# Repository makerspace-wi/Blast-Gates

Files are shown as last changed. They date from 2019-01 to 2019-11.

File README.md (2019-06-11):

# Blast-Gates
Schieberanordnung für Absauganlage

Die letzte geplante Variante konnte leider nicht realisiert werden - ein alternativ Vorschlag wurde erarbeitet.
<br>
Die Arbeiten wurden jetzt vollständig vom 'Dream-Team' übernommen und das Konzept wie folgt geändert:
<br><br>
Zum Einsatz kommt eine 'Distribution Box' aus Holz mit 6 Öffnungen, wobei die obere Öffnung eine Plexiglasscheibe sein wird, durch die man ins Innere schauen und ggf. zur Reinigung öffnen kann.

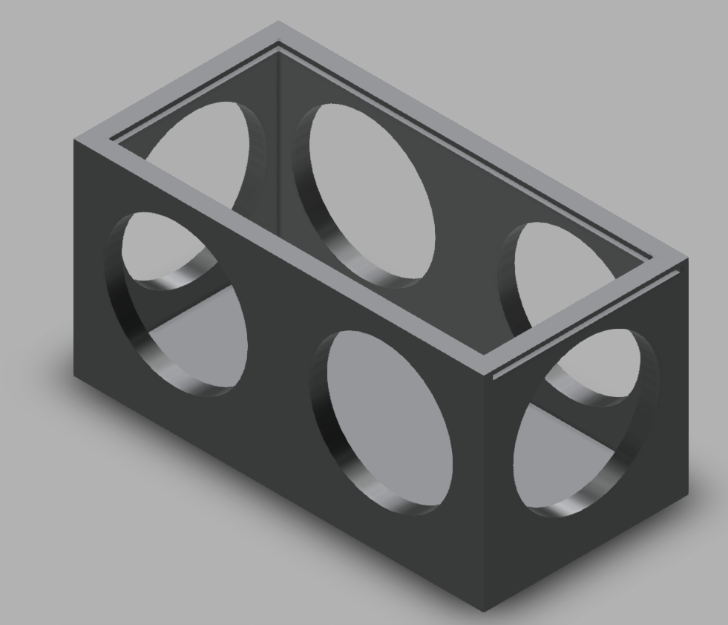
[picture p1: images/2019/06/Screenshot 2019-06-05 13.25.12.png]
  

Eine Öffnung wird an die Absaugeinrichtung angschlossen, jeweils eine von 4 Öffnungen gehen an die Formatkreissäge, die Bandsäge, den Abrichthobel, die Schleifvorrichtung und die letzte Öffnung ist für einen Handabsaugschlauch vorgesehen.<br>
Als Anschlüsse haben wir uns für industriell gefertigte, manuelle Schieber aus Aluguß/Stahlblech entschieden.

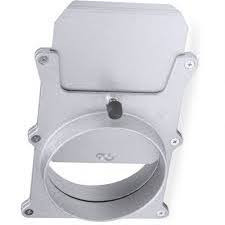
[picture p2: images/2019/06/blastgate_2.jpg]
  

In der ersten Ausbaustufe sollen die Schieber noch per Hand geöffnet/geschlossen werden, allerdings wird die Stellung jeder Klappe über Mikroschalter an eine Steuereinheit gemeldet.<br>
Zu einem späteren Zeitpunkt sollen die Schieber per Spindelantrieb elektronisch auf und zu gefahren werden.

<video width="320" height="240" controls>
  <source src='images/2019/06/BlastGateMetall.mp4' type="video/mp4">
</video>

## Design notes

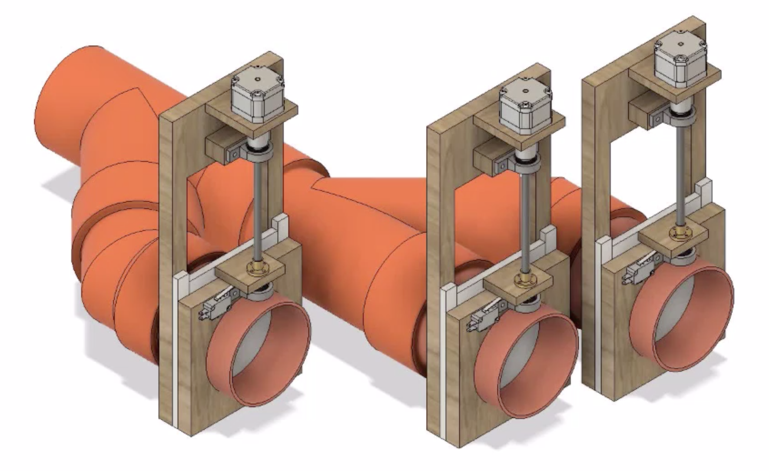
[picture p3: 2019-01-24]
images/2019/01/Screenshot 2019-01-24 10.25.47.png

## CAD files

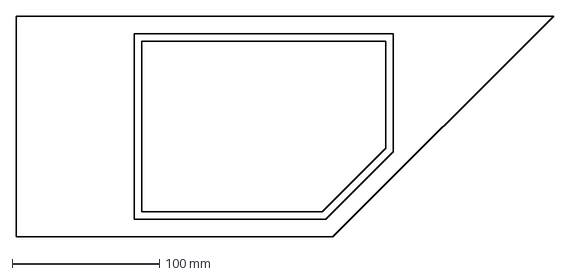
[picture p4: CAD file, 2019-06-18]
doc/AbsaubungsVerteiler/SeitenplatteLiAussparung.dxf
365.0 x 150.0 mm

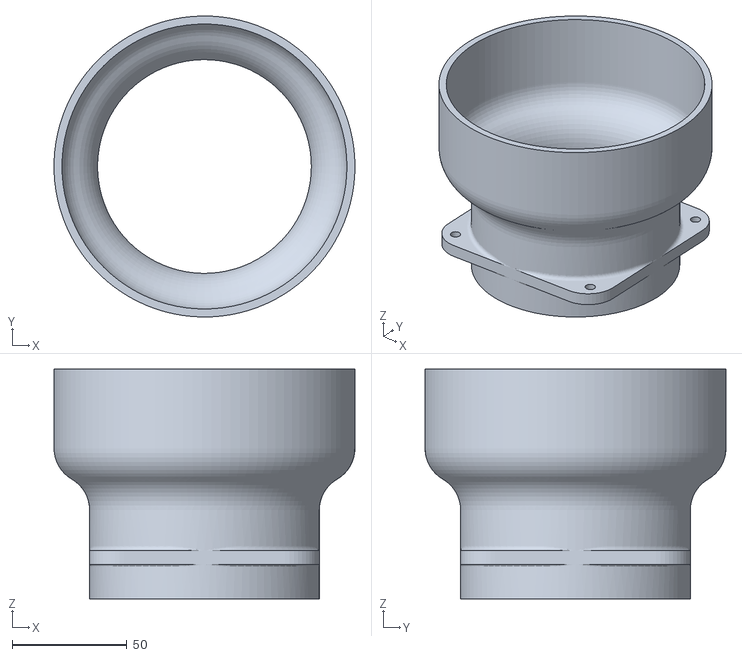
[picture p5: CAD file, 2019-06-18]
doc/AbsaubungsVerteiler/Reduzierstücke_mit_Halter.stl
131.0 x 131.0 x 100.0

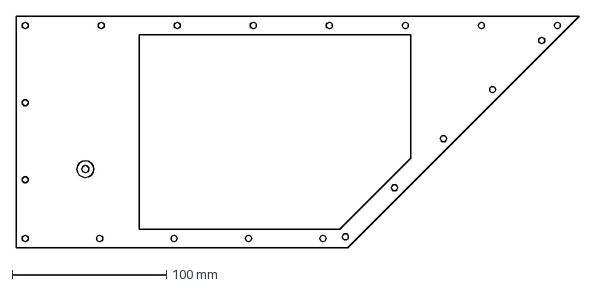
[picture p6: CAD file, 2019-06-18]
doc/AbsaubungsVerteiler/SeitenplatteLiGeh.dxf
365.0 x 150.0 mm

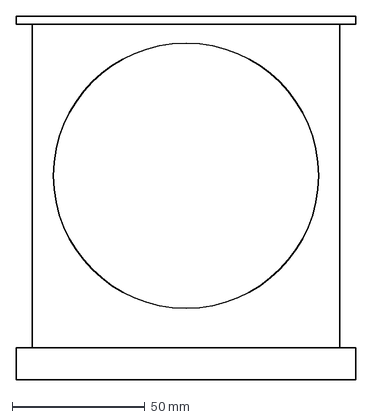
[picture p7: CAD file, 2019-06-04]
doc/AbsaubungsVerteiler/SeitenteilRechts.dxf
128.0 x 137.2 mm

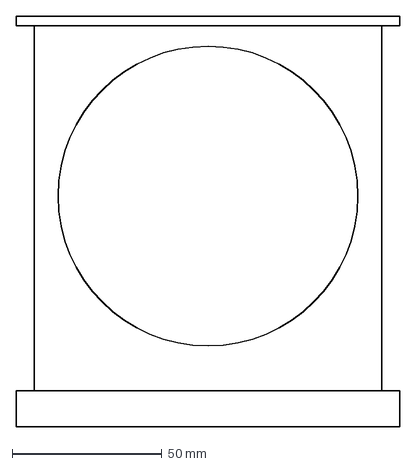
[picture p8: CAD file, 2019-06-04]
doc/AbsaubungsVerteiler/SeitenteilLinks.dxf
128.0 x 137.0 mm

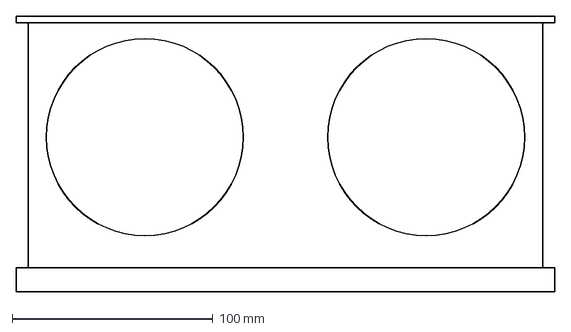
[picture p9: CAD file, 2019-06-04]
doc/AbsaubungsVerteiler/SeitenteilGross.dxf
268.0 x 137.2 mm

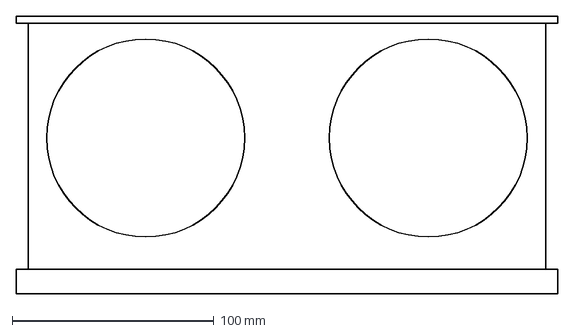
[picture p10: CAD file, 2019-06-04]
doc/AbsaubungsVerteiler/SeitenteilGrossN.dxf
268.0 x 137.2 mm

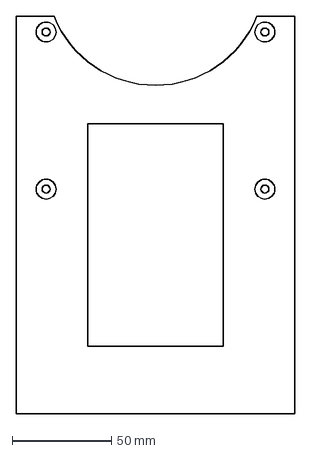
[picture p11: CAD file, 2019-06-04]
doc/AbsaubungsVerteiler/EndSchalterMount.dxf
140.0 x 200.0 mm

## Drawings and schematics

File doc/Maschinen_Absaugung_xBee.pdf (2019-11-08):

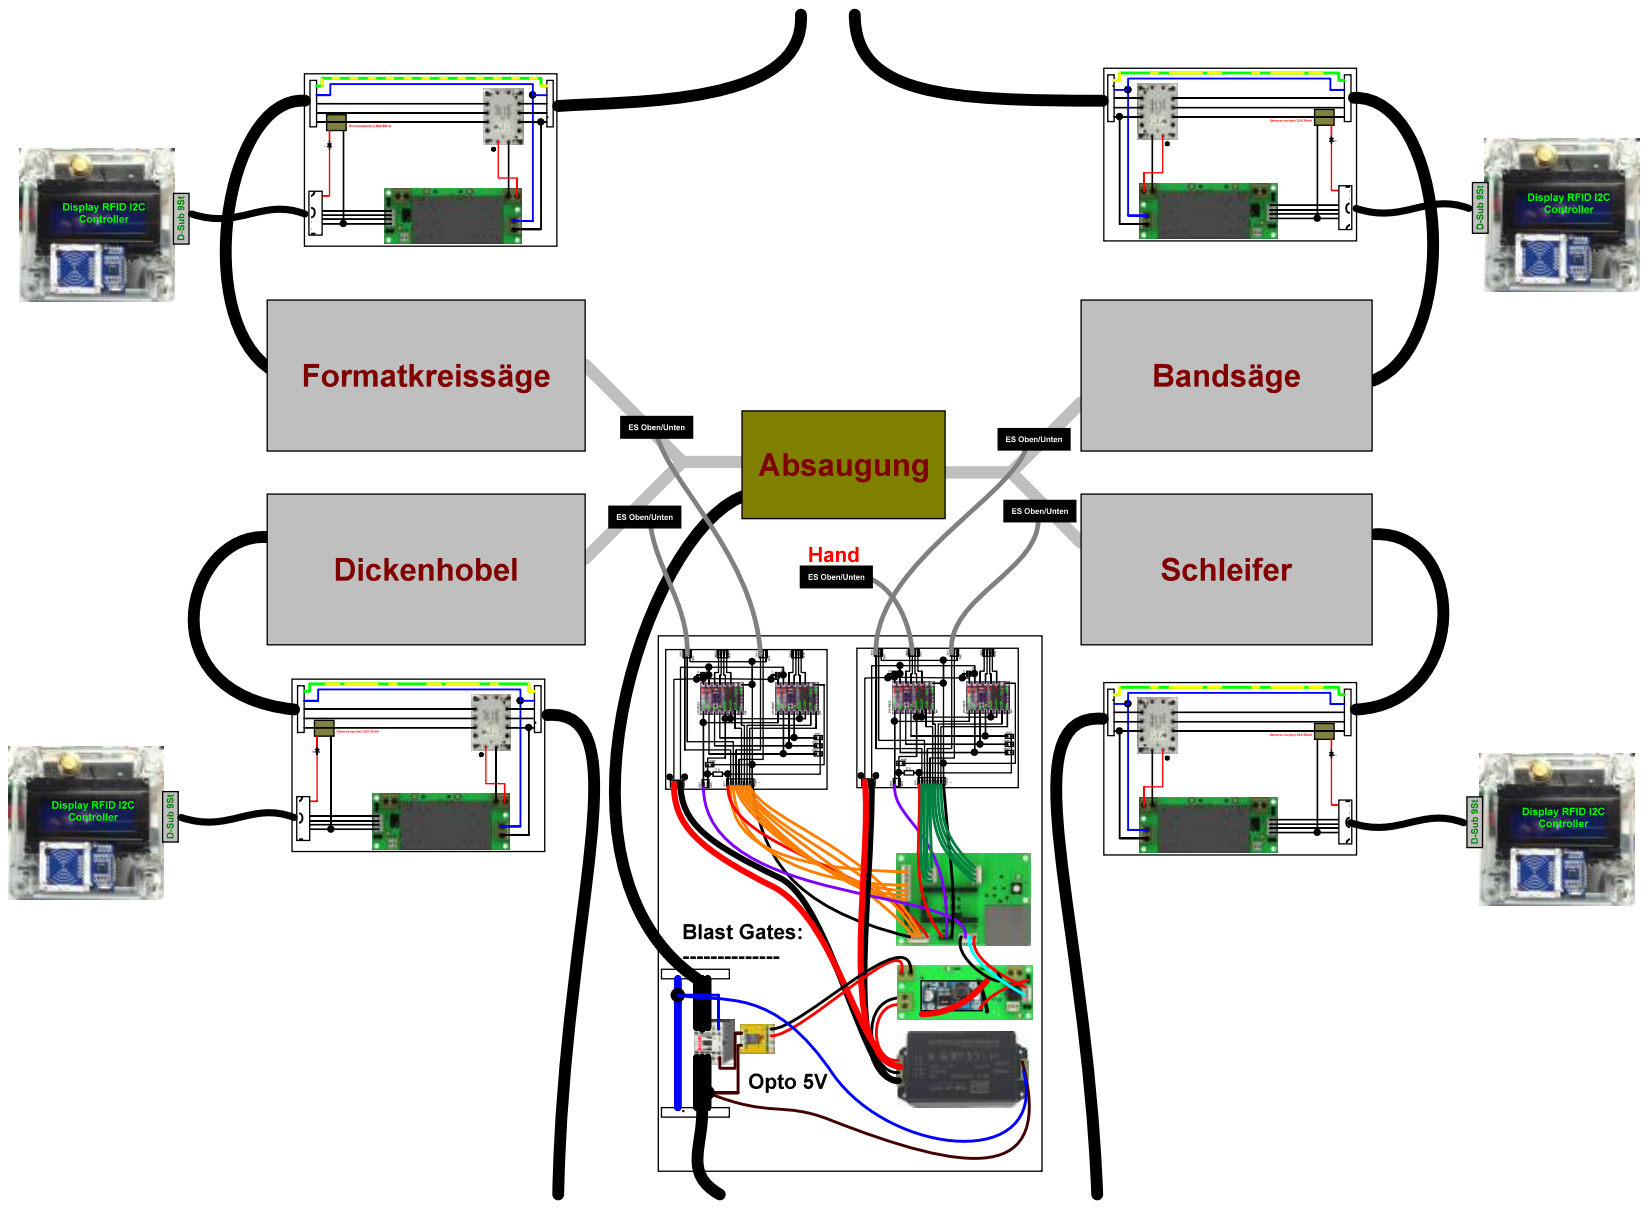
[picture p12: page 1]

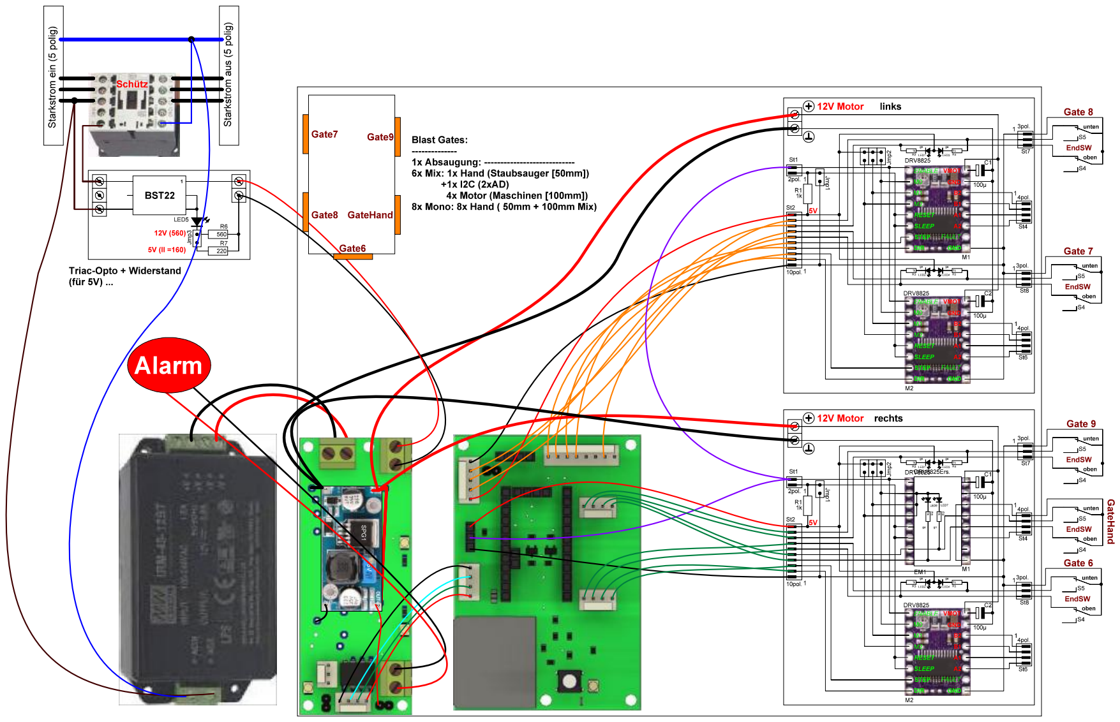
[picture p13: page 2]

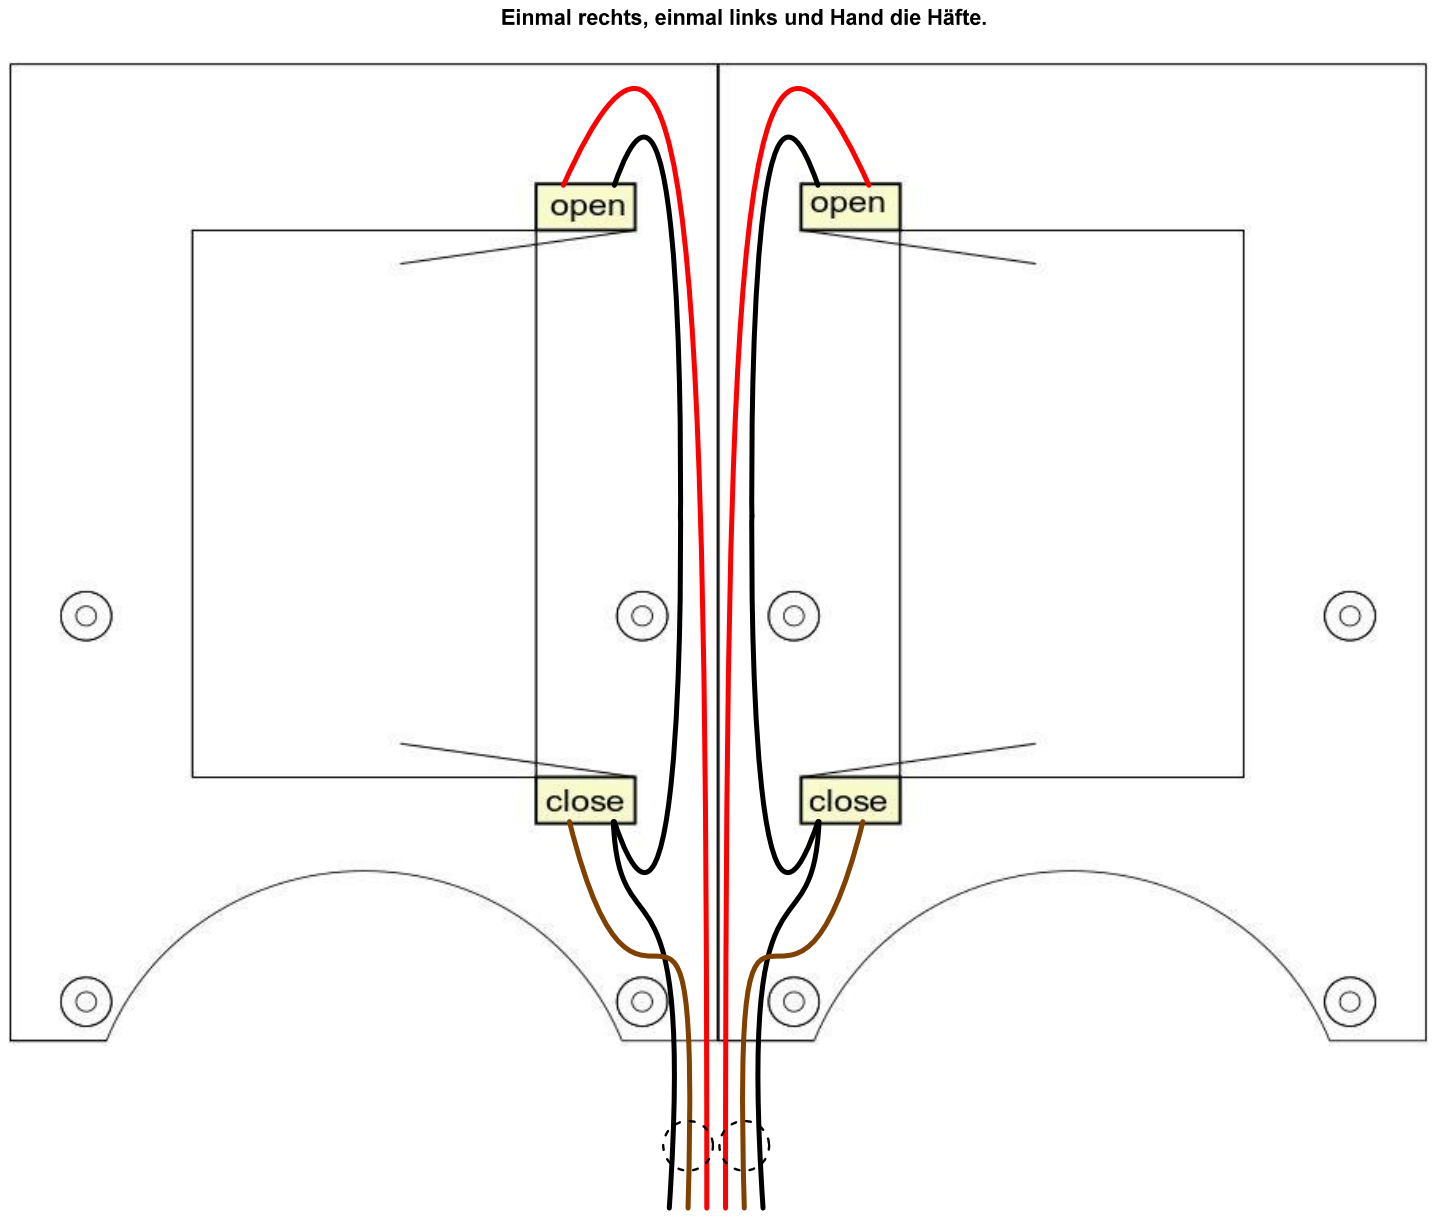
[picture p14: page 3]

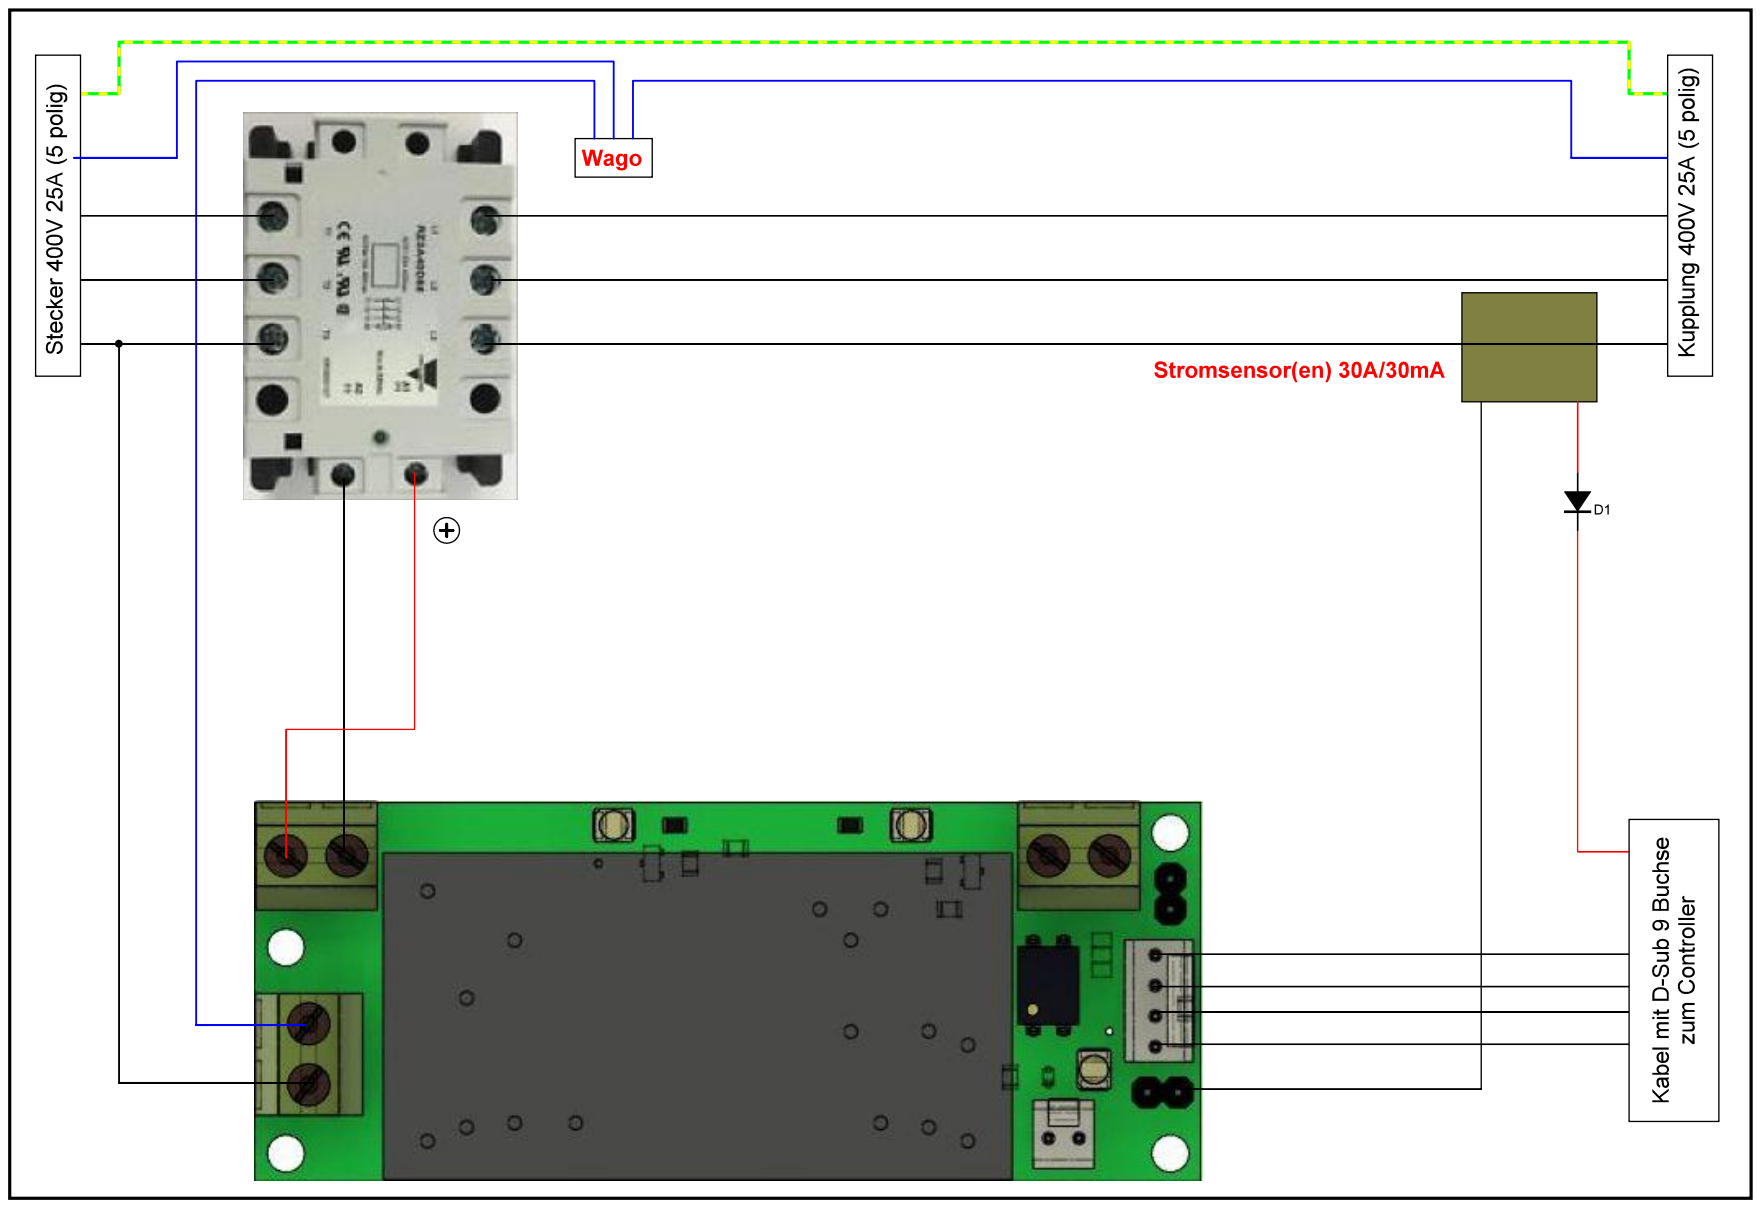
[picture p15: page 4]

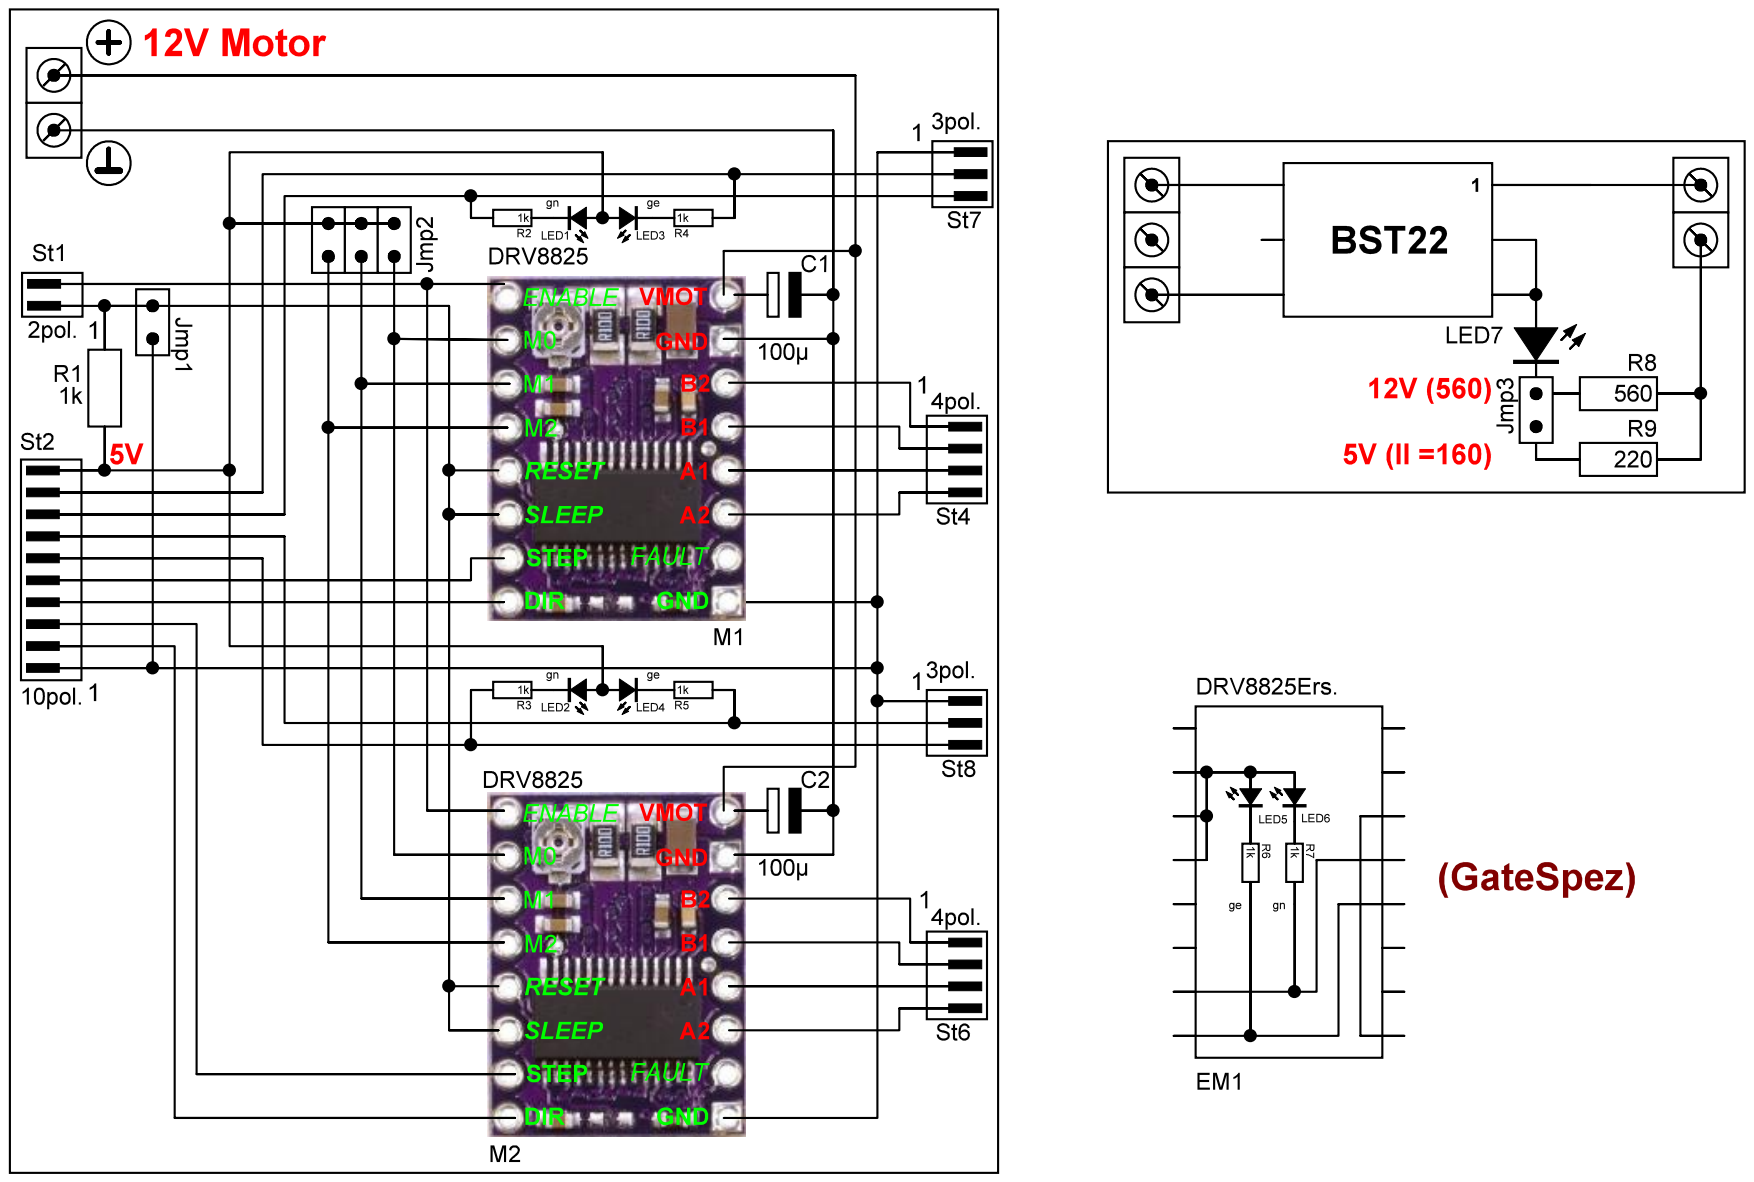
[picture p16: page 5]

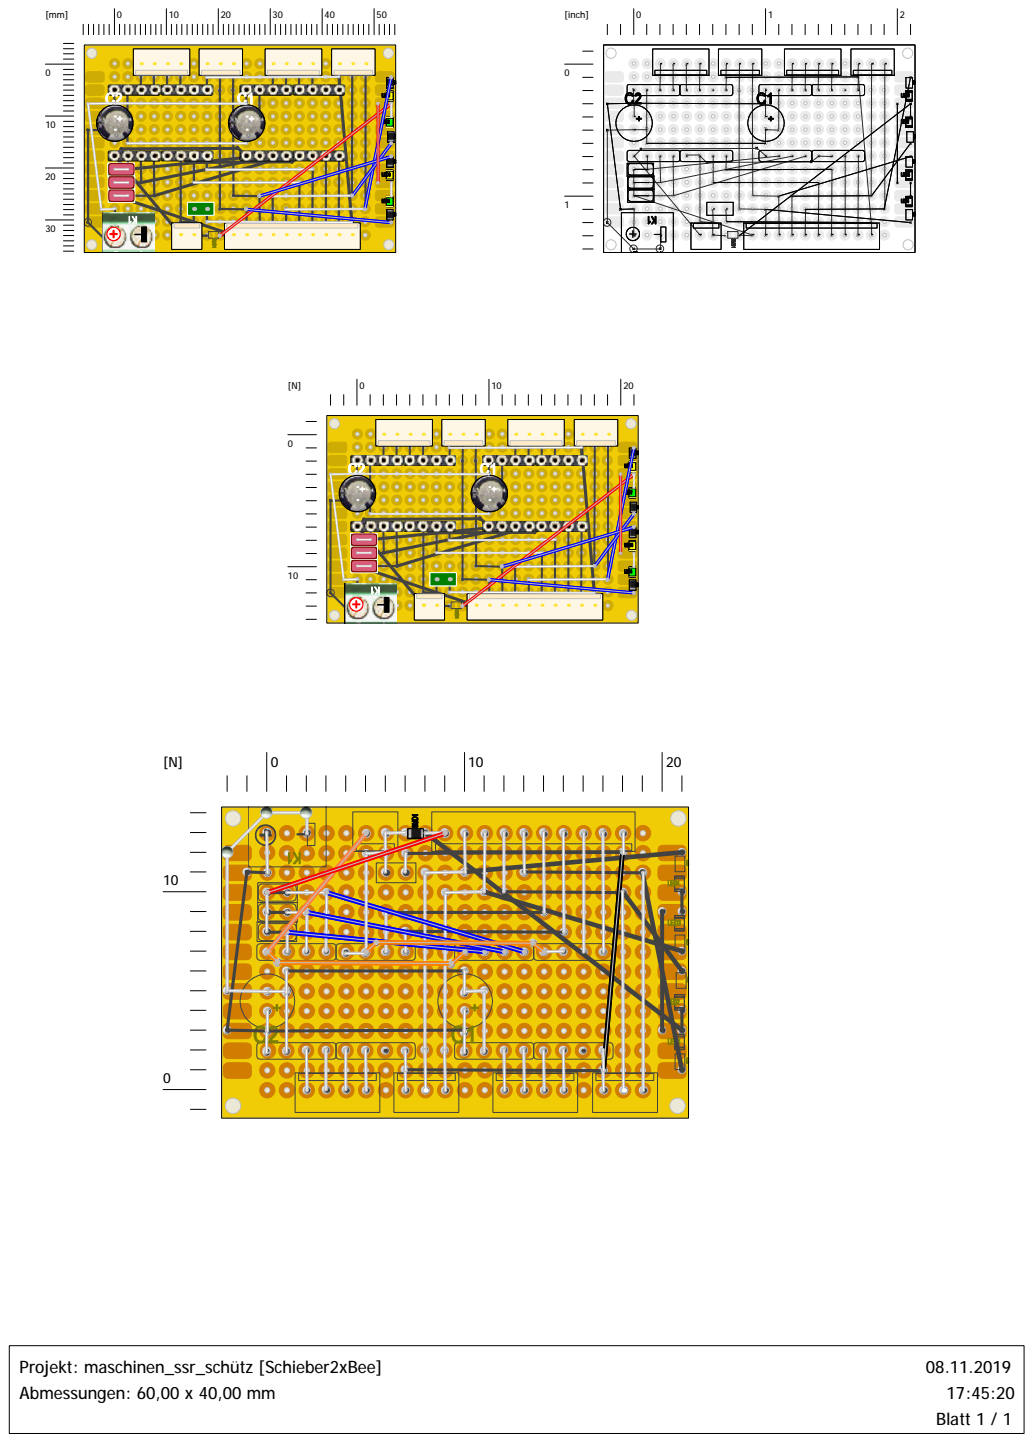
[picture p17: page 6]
[inch]; Projekt: maschinen_ssr_schütz [Schieber2xBee] Abmessungen: 60,00 x 40,00 mm; 08.11.2019 17:45:20 Blatt 1 / 1

0

0

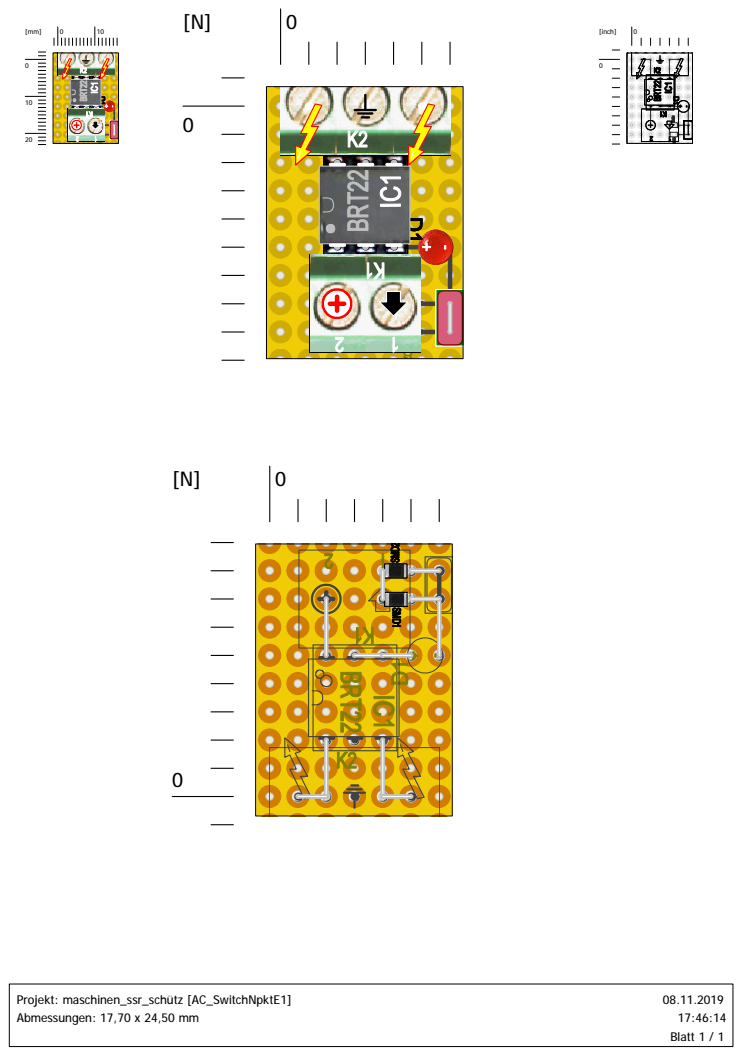
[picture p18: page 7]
[inch]; Projekt: maschinen_ssr_schütz [AC_SwitchNpktE1] Abmessungen: 17,70 x 24,50 mm; 08.11.2019 17:46:14 Blatt 1 / 1

0

[N]

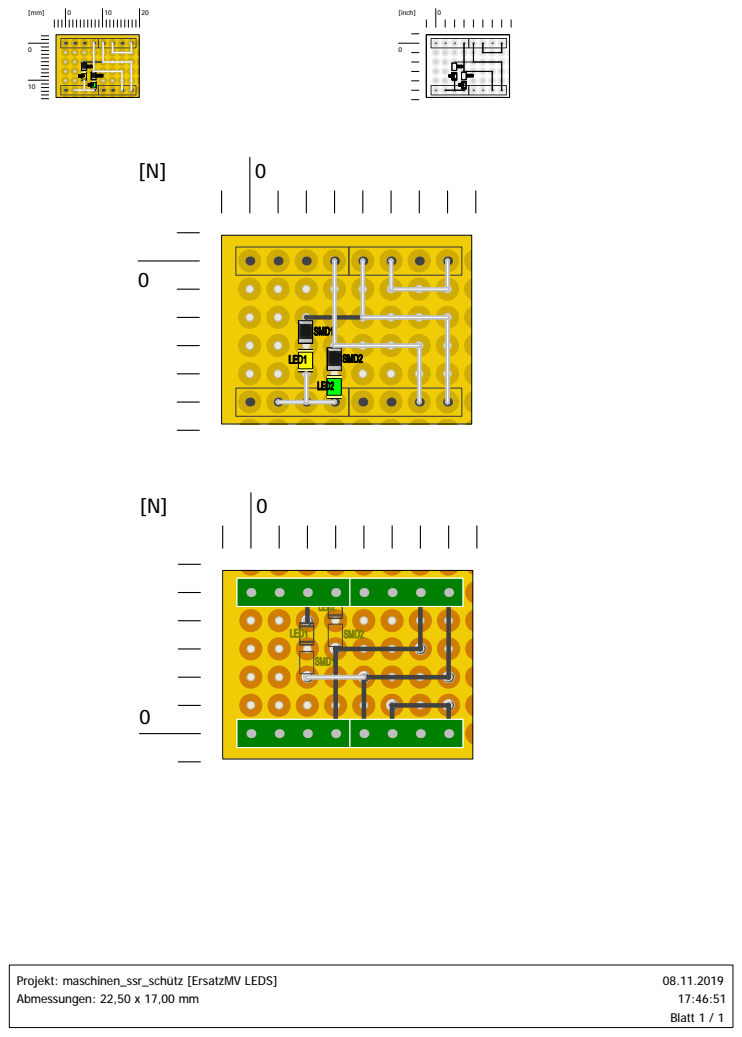
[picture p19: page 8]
[inch]; 08.11.2019 17:46:51 Blatt 1 / 1

Projekt: maschinen_ssr_schütz [ErsatzMV LEDS]
Abmessungen: 22,50 x 17,00 mm

GeräteVerdrahtung | Seite 1 / 1
Benennung K2 4polig Strommessung | D-Sub | D-Sub Buchse Kabel
5V | 4 | rot | 1 | bn | sw
| | | 2 | rt | bn
| | | 3 | or | rt
A3 | 3 | orange | 4 | ge | or
A2 | 2 | braun | 5 | gn | ge
Strom + | rt | 6 | bl | gn
GND | 1 | sw
| | rot | 7 | li | rs
| | schwarz | 8 | gr | li
| | sw | 9 | sw | ws
Benennung K1 5polig | K3 8polig | (Farbe) D-Sub
5V | 5 | rot | 1
SCL | 4 | orange | 2
SDA | 3 | gelb | 3
SCK | 7 | blau | 4
MISO | 5 | gelb | 5
MOSI | 6 | grün | 6
SDA | 8 | violet | 7
RST | 2 | braun | 8
GND | 1 | schwarz | 9

### Buchse / Stecker

### Buchse / Stecker

BlastGateEM_Verdrahtung | Seite 1 / 1
PinNr. Netzteil | Pin Out Controller Ardu Pin | Pin In SM-Platine Li | Pin Out | Pin In SM-Platine Re Pin Out | PinNr. | EndPos
K1P1 L | ~220V;12V
K1P2 N | ~220V;12V
K2P1 SSR1 | 24V 4A
K2P2 | Vcc | 5V – (24V)
K3P1 SSR2 | 24V 4A
K3P2 | Vcc | 5V – (24V)
K1P1 | Digital (INT) | 2 | St2P7 Gate 6 closed | St5P2 | St5P2
K1P2 | Digital (PWM) | 5 | St2P6 Gate 6 open | St5P3 | St5P3
K1P3 | Digital | 7 | St2P2 Dir | Gate 6 SM St6 | St6P1-4 | B1;B2;A1;A2 K1P4 | Digital (PWM) | 9 | St2P3 Step
K5P1 | GND | GND | K2P1 | GND | St3&4&5P1 | GND
K5P2 SSR1 | K2P2 | OptSSR (AD2) | A2
K5P3 SSR2 | K2P3 | Alarm (AD3) | A3
K5P4 | Vcc | 5V (DC/DC) | K2P4 | Vcc
K4P1 | GND | St2P1 | GND
K4P2 | Digital (PWM) | 6 | St1P2 Enable SM | St1P2 Enable SM
K4P3 | Vcc | St2P10 | VCC
K5P1 | Analog | A0 | St2P9 Gate 9 closed | St3P2 | St3P2
K5P2 | Analog | A1 | St2P8 Gate 9 open | St3P3 | St3P3
K5P3 | Analog | A6 | St2P5 (Step) | Gate 9 SM St4 | St4P3 | Gate H open
K5P4 | Analog | A7 | St2P4 (Dir) | St4P2 | Gate H closed
K7P1 | GND | St2P1 | GND | St3&5P1 | GND
K7P2 | 3 | St2P9 Gate 8 closed | St3P2 | St3P2
K7P3 | SDA (AD4) | A4 | St2P8 Gate 8 open | St3P3 | St3P3
K7P4 | SCL (AD5) | A5 | St2P6 Gate 7 open | St5P3 | St5P3
K7P5 | Vcc | St2P10 | Vcc
K9P1 | Vcc
K9P2 | Digital | 4 | St2P7 Gate 7 closed | St5P2 | St5P2
K9P3 | GND
K9P4 | - | -
K9P5 | Digital | 12 | St2P4 Dir | Gate 8 SM St4 | St4P1-4 | B1;B2;A1;A2 K9P6 | Digital (PWM) | 11 | St2P5 Step
K9P7 | Digital | 13 | St2P2 Dir | Gate 7 SM St6 | St4P1-4 | B1;B2;A1;A2 K9P8 | Digital (PWM) | 10 | St2P3 Step

S
c

### hrittm

otor

A
n
ste

u
eru

n
g re

c
hts

S
c

### hrittm

otor

A
n
ste

u
eru

n
g lin

k
s

Digital (INT, PWM)

Nur Analoge
Eingänge

BlasgatePosition | Seite 1 / 1
Mini | Blast Gate Hand alles manuell | Mini | Blast Gate Schrittmotor automatisch + Hand
6 K4P2 | Li / St1 | 2 | Enable | 6 K4P2 | Li / St1 | 2 Enable
K7P1

Li / St2

1 GND
Li / St3
1 GND | Gate 8 | K7P1

Li / St2

1 GND
Li / St3
| | | | | | 1 GND | Gate 8
3 K7P2 | 9 | ← | 2 EndPos closed | 3 K7P2 | 9 <== | 2 EndPos closed open
A4 K7P3 | 8 | ← | 3 EndPos open | A4 K7P3 | 8 ↔ | 3 | I2C SDA
Absaugung | K7P5 | 10 | 5V | K7P5 | 10 5V

Li / St4

| | | 1 B2
Li / St4
1 B2 | M2 2 B1 | 2 B1
11 K9P6 | 5 | Step | 3 A1 | 11 K9P6 | 5 Step | 3 A1 | M1 12 K9P5 | 4 | Dir | 4 A2 | 12 K9P5 | 4 Dir | 4 A2

Li / St5

1 GND Gate 7
Li / St5
| | | | | | | | 1 GND | Gate 7
4 K9P2 | 7 | ← | 2 EndPos closed | 4 K9P2 | 7 <== | 2 EndPos closed open
Bandsäge | Schleifer | A5 K7P4 | 6 | ← | 3 EndPos open | A5 K7P4 | 6 --> | 3 | I2C SLC
Gate 7 | Gate 9

Li / St6

| | | | | 1 B2
Li / St6
1 B2 | M2 2 B1 | 2 B1
10 K9P8 | 3 | Step | 3 A1 | 10 K9P8 | 3 Step | 3 A1 | M1 13 K9P7 | 2 | Dir | 4 A2 | 13 K9P7 | 2 Dir | 4 A2
6 K4P2 | Re / St1 | 2 | Enable | 6 K4P2 | Re / St1 | 2 Enable
K4P1

Re / St2

1 GND
Re / St3
1 GND | Gate 9 | K4P1

Re / St2

1 GND
Re / St3
1 GND | Gate 9
A0 K5P1 | 9 | ← | 2 EndPos closed | A0 K5P1 | 9 <== | 2 EndPos closed open
A1 K5P2 | 8 | ← | 3 EndPos open | A6 K5P3 | 8 ← | 3 | Gate H closed
K4P3 | 10 | 5V | | K4P3 | 10 5V
Dickenhobel | Hand
Re / St4

1 B2 GND
Re / St4
1 B2 | M2 Gate 8 | Gate Hand | 2 B1 | closed | 2 B1
A6 K5P3 | 5 | Step | 3 A2 | open | 5 K1P2 | 5 Step | 3 A2 | M1 A7 K5P4 | 4 | Dir | 4 A1 | Gate H | 2 K1P1 | 4 Dir | 4 A1

Re / St5
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

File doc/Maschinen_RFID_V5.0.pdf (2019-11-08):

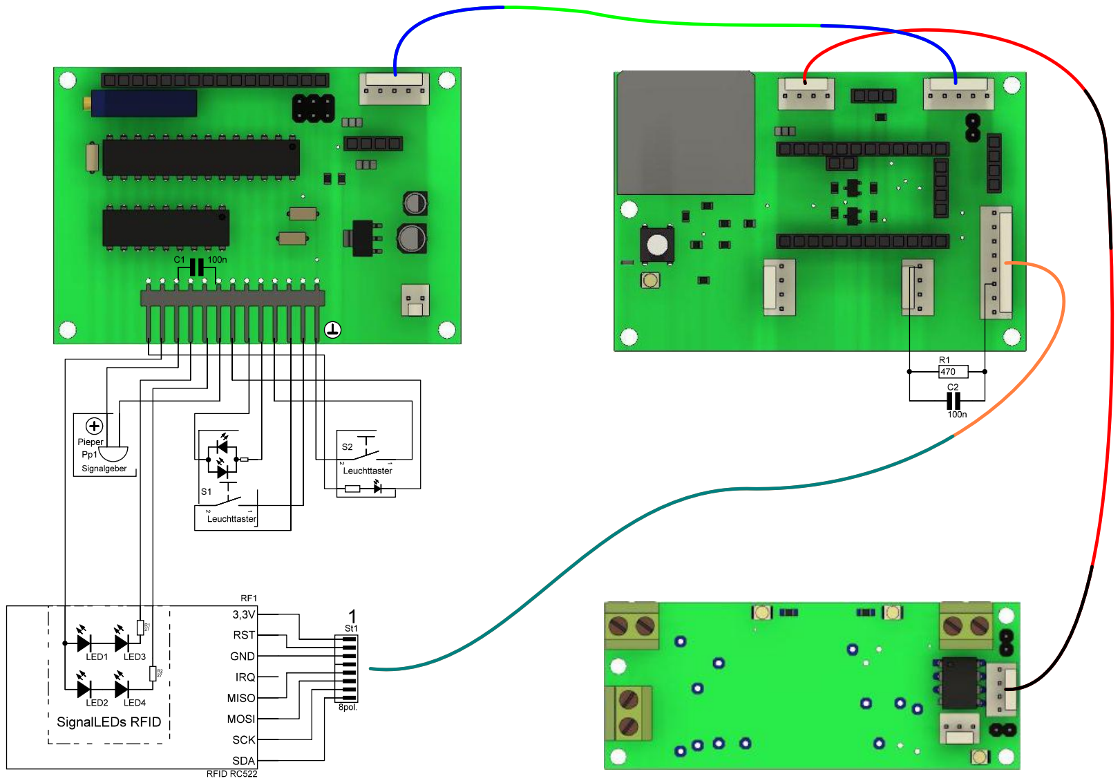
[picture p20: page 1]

J4

K2

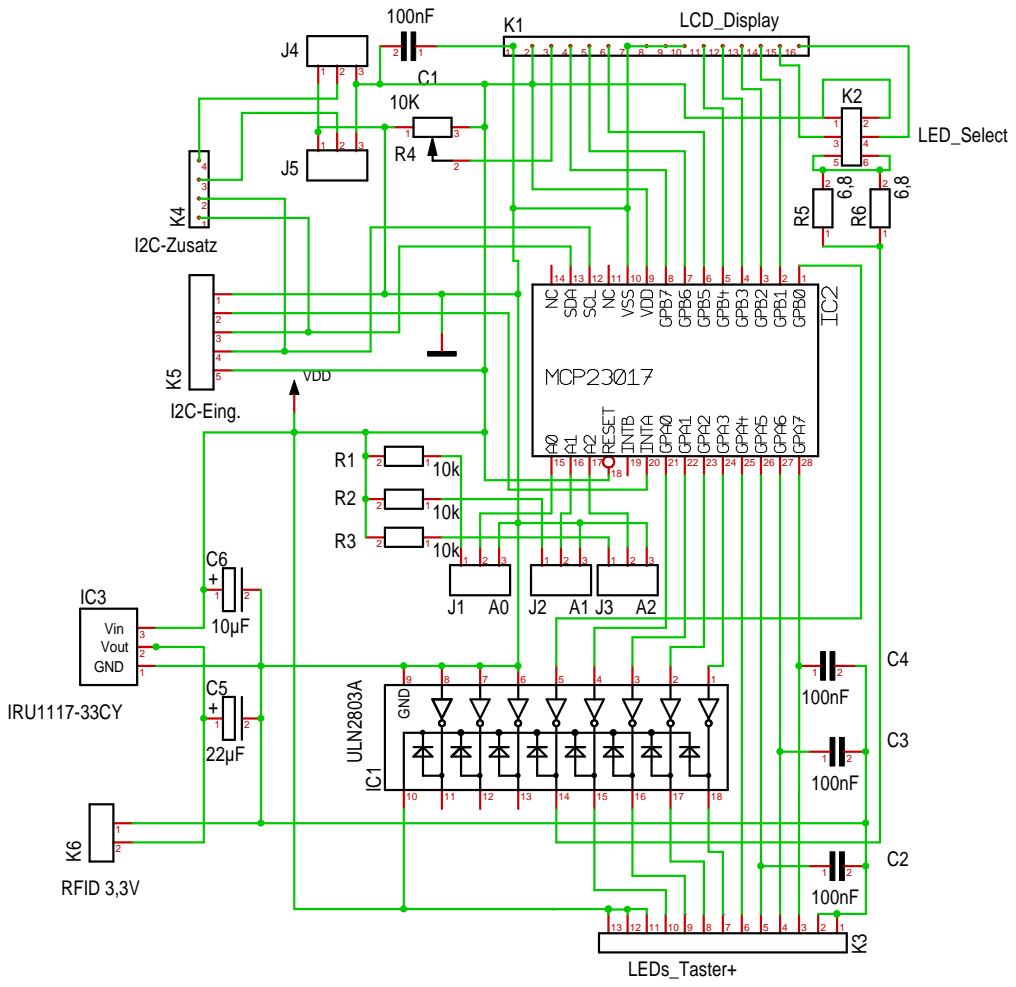
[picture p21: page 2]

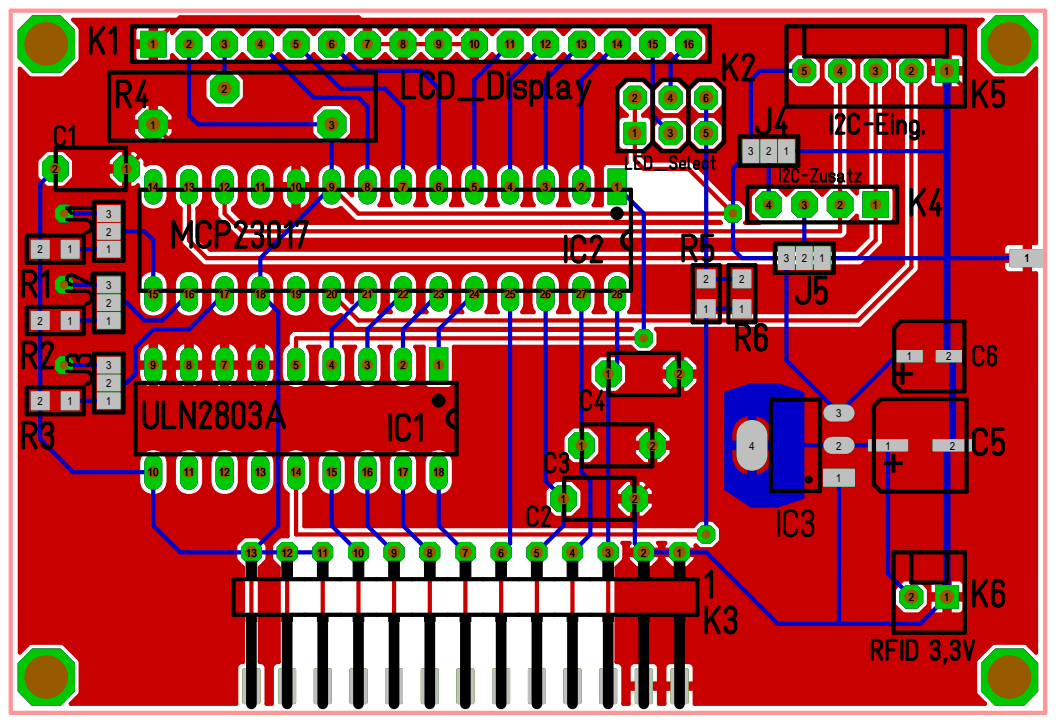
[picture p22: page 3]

## 1µF C3

## 1µF C2

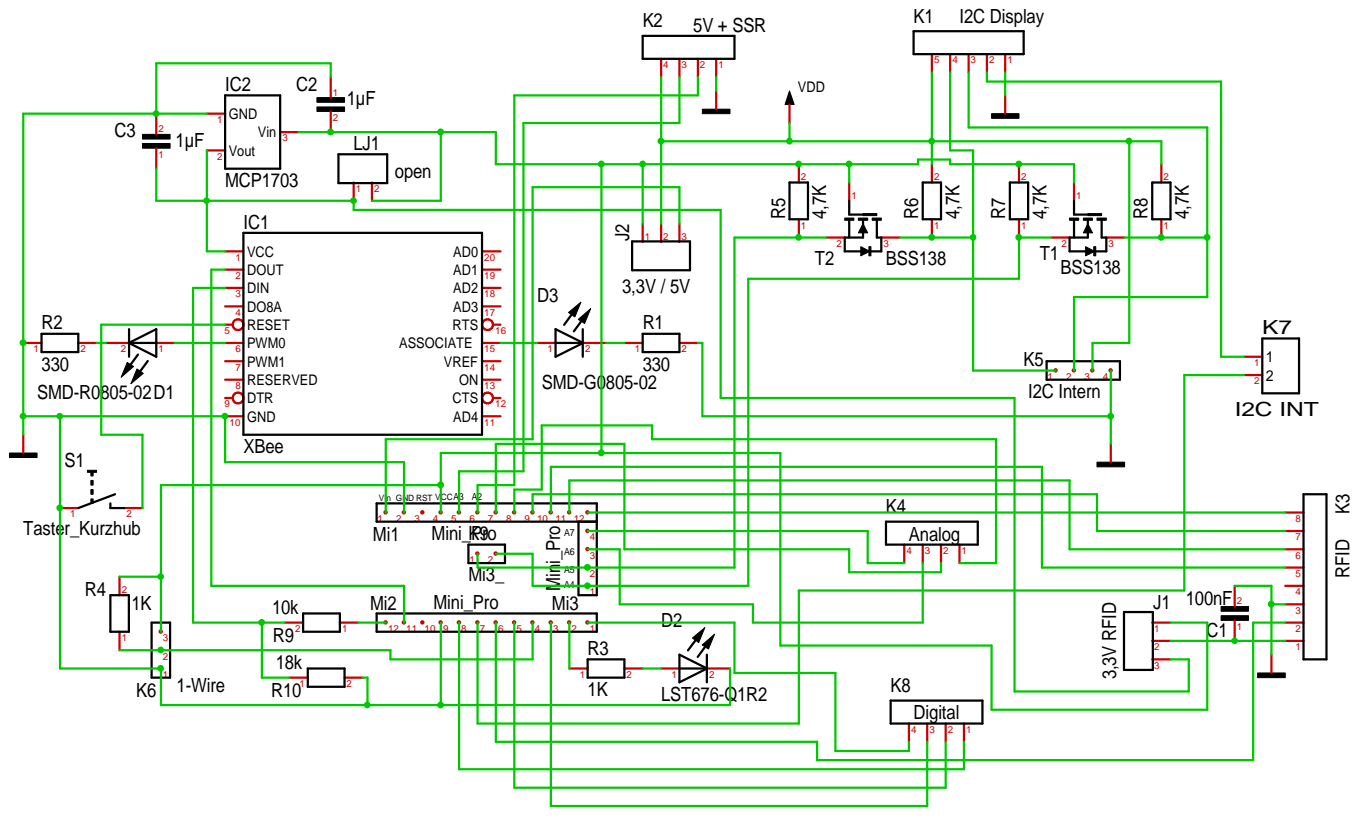
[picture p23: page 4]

1-

# Wire

I2C Intern; RFID; V + SSR; play

1 | 1 | DCDC 5V
| K6


SSR1 | SSR2 230V AC


Benennung K2 4polig Strommessung | D-Sub | D-Sub Buchse Kabel
5V | 4 | rot

### 1 bn 2 rt 3 or

A3 | 3 | orange | 4 | ge
A2 | 2 | braun | 5 | gn
Strom + | rt | 6 | bl
GND | 1 | sw
| | rot | 7 | li
| | schwarz | 8 | gr
| | sw | 9 | sw
Benennung K1 5polig | K3 8polig | (Farbe) D-Sub
5V | 5 | rot | 1
SCL | 4 | orange | 2
SDA | 3 | gelb | 3
SCK | 7 | blau | 4
MISO | 5 | gelb | 5
MOSI | 6 | grün | 6
SDA | 8 | violet | 7
RST | 2 | braun | 8
GND | 1 | schwarz | 9

Buchse / Stecker

Buchse / Stecker

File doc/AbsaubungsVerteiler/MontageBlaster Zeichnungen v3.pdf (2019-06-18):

Michael Muehl 116

Dept. | Technical reference | Created by 17.06.2019 | Approved by

Document type | Document status

Title MontageBlaster | DWG No.

Rev. | Date of issue | Sheet

Michael Muehl 126

Dept. | Technical reference | Created by 17.06.2019 | Approved by

Document type | Document status

Title MontageBlaster | DWG No.


Dept. | Technical reference | Created by Michael Muehl 17.06.2019 | Approved by

Document type | Document status

Title MontageBlaster | DWG No.

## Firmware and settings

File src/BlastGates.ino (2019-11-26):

/* DESCRIPTION
  ====================
  control 4(1) blast gates for vacuum cleaner for 4 machines and manuell

  the gate is driven by hand, controller and xBee for
  comunication with machines (ID):
  Formatkreissaege (6), Bandsaege (7), Dickenhobel (8), Schleifer (9)
  and a gate for manuell cleaning (H)
 -Parameter of our system-------------:
  Commands to Raspi --->
  'BGATE' - from xBee (=Ident)
  'POR'   - machine power on reset (Ident;por)

  ---------- (_=6,7,8,9)
  'g_o'   - Gate is Open
  'g_w'   - Gate is waiting for login
  'gho'   - Gate By hand is open (Manuell)
  'g_c'   - Gate is Closed
  'ghc'   - gate By hand is closed
  'err'   - Error message is following ('ERR:G7O')
  'gok'   - all blast gates are ok, in write position

  Commands from Raspi <---
  'time'  - format time33.33.33 33:33:33
  'setrt' - set RepeaT messages
  'setwt' - set WaiT for open until login in sec

  ---------- (_=6,7,8,9)
  'li_'   - log in for machine
  'lo_'   - log out for machine
  'do_'   - Dust collector On for machine
  'df_'   - Dust collector oFf for machine
  'ng_'   - No Gate is available

  last change: 20.11.2019 by Michael Muehl
  changed: open before login, error after 30sec for gate MA 6-9
	*/
#define Version "1.2" // (Test =1.1 ==> 1.2)

//#define _TASK_MICRO_RES // only for SM
// ---------------------
#include <Arduino.h>
#include <TaskScheduler.h>

// PIN Assignments
// Steps for the stepper
#define STEPS_G6  9	// stepper steps Gate 6
#define STEPS_G7 10 // stepper steps Gate 7
#define STEPS_G8 11	// stepper steps Gate 8
#define STEPS_G9 A6	// stepper steps Gate 9 [not for SM]
// Direction of movement
#define DIR_G6    7	// dir stepper Gate 6
#define DIR_G7   13	// dir stepper Gate 7
#define DIR_G8   12	// dir stepper Gate 8
#define DIR_G9   A7	// dir stepper Gate 9 [not for SM]
// enable all steppers
#define enaStGate 6	// enable stepper Gates

// this pin should connect NOT to Ground when want to stop the motor
#define EndPoG6C  2 // Endpostion Gate 6 close
#define EndPoG6O  5 // Endpostion Gate 6 open (only with endswitch open)
#define EndPoG7C  4 // Endpostion Gate 7 close
#define EndPoG7O A5 // Endpostion Gate 7 open (only with endswitch open)
#define EndPoG8C  3 // Endpostion Gate 8 close
#define EndPoG8O A4 // Endpostion Gate 8 open (only with endswitch open)
#define EndPoG9C A0 // Endpostion Gate 9 close
#define EndPoG9O A1 // Endpostion Gate 9 open (only with endswitch open)
#define EndPoGHC A6 // Endpostion Gate by hand close (Only analog input)
#define EndPoGHO A7 // Endpostion Gate by hand open (Only analog input)

#define REL_Vac  A2 // Relais Dust on / off  (Dust Collector)
#define SIGError A3 // SIGError for error
#define BUSError  8 // Bus error
#define xbeError  8 // Bus error (13)

// Task speck
// Motor steps per revolution. Most steppers are 200 steps or 1.8 degrees/step
#define MOTOR_STEPS 200
// Microstepping mode. If you hardwired it to save pins, set to the same value here.
#define MICROSTEPS 4

#define maxSPEED  50  // [50] µs
#define minSPEED 500  // [500] µs
// Acceleration and deceleration values are always in FULL steps / s^2
#define MOTOR_ACCEL (minSPEED - maxSPEED)
#define MOTOR_DECEL (minSPEED - maxSPEED)

#define gateStepsMM 25 // steps to drive 1 mm
#define gateOPEN  HIGH // direction for opening gate

// DEFINES
#define porTime         5 // wait seconds for sending Ident + POR
#define repMES          1 // repeat commands
#define divTime         4 // divider for time

Scheduler runner;

// Callback methods prototypes
void checkXbee();        // Task connect to xBee Server
void repeatMES();        // Task to repeat messages
void retryPOR();         // Task connect to xBee Server

void gateStart();        // Task start with closed all
void gateChange();       // Task check changes
void gateMA();           // Task control maschines
void gateHA();           // Task control hand gate

// TASKS
Task tC(TASK_SECOND / 2, TASK_FOREVER, &checkXbee);     // 500ms
Task tB(TASK_SECOND * 5, TASK_FOREVER, &retryPOR);      // 100ms, task for debounce
Task tR(TASK_SECOND / 2, 0, &repeatMES);                // 500ms * repMES repeat messages

// --- Blast Gates ----------
Task tGC(TASK_SECOND / divTime, TASK_FOREVER, &gateChange);  // task for Gate Change check
Task tGM(1, TASK_ONCE, &gateMA);                             // task for Gate machines
Task tGH(1, TASK_ONCE, &gateHA);                             // task for Gate hand

// VARIABLES
boolean noGAT6 = LOW; // bit no gate 6
boolean dustC6 = LOW; // bit dust Collector for machine 6 = HIGH
boolean logIM6 = LOW; // bit log in machine 6 = HIGH
boolean gate6O = LOW; // bit gate 6 open = HIGH
boolean gate6C = LOW; // bit gate 6 close = HIGH

boolean noGAT7 = LOW; // bit no gate 7
boolean dustC7 = LOW; // bit dust Collector for machine 7 = HIGH
boolean logIM7 = LOW; // bit log in for machine 7 = HIGH
boolean gate7O = LOW; // bit gate 7 open = HIGH
boolean gate7C = LOW; // bit gate 7 close = HIGH

boolean noGAT8 = LOW; // bit no gate 8
boolean dustC8 = LOW; // bit dust Collector for machine 8 = HIGH
boolean logIM8 = LOW; // bit log in machine 8 = HIGH
boolean gate8O = LOW; // bit gate 8 open = HIGH
boolean gate8C = LOW; // bit gate 8 close = HIGH

boolean noGAT9 = LOW; // bit no gate 9
boolean dustC9 = LOW; // bit dust Collector for machine 9 = HIGH
boolean logIM9 = LOW; // bit log in machine 9 = HIGH
boolean gate9O = LOW; // bit gate 9 open = HIGH
boolean gate9C = LOW; // bit gate 9 close = HIGH

boolean gateHO = LOW; // bit gate By hand open = HIGH
boolean gateHC = LOW; // bit gate By hand close = HIGH

byte stepSP = 0;      // steps for start position

byte errCount = 0;      // how many errors are active
int gateNR = 0;         // "0" = no gates, 6,7,8,9 with gate
int dustWaitT = 0;      // counter how long dust wait time
int open4log6 = -1;      // counter how long gate 6 open for login
int open4log7 = -1;      // counter how long gate 7 open for login
int open4log8 = -1;      // counter how long gate 8 open for login
int open4log9 = -1;      // counter how long gate 9 open for login

// Serial with xBee
String inStr = "";      // a string to hold incoming data
String IDENT = "";      // Machine identifier for remote access control
String SFMes = "";      // Send For repeatMES
int waitGO = 0;         // wait for gate open
byte plplpl = 0;        // send +++ control AT sequenz
byte getTime = porTime;

// ======>  SET UP AREA <=====
void setup() {
  //init Serial port
  Serial.begin(57600);  // Serial
  inStr.reserve(40);    // reserve for instr serial input
  IDENT.reserve(5);     // reserve for IDENT serial output

  // PIN MODES
  // Stepper -----------
  pinMode(STEPS_G6, OUTPUT);
  pinMode(STEPS_G7, OUTPUT);
  pinMode(STEPS_G8, OUTPUT);
//  pinMode(STEPS_G9, OUTPUT); // not on ES

  pinMode(DIR_G6, OUTPUT);
  pinMode(DIR_G7, OUTPUT);
  pinMode(DIR_G8, OUTPUT);
//  pinMode(DIR_G9, OUTPUT); // not on ES

  pinMode(enaStGate, OUTPUT);

  pinMode(EndPoG6C, INPUT);
  pinMode(EndPoG6O, INPUT); // Switch input ES
  pinMode(EndPoG7C, INPUT);
  pinMode(EndPoG7O, INPUT); // Switch input ES
  pinMode(EndPoG8C, INPUT);
  pinMode(EndPoG8O, INPUT); // Switch input ES
  pinMode(EndPoG9C, INPUT);
  pinMode(EndPoG9O, INPUT); // Switch input ES

  pinMode(EndPoGHC, INPUT);
  pinMode(EndPoGHO, INPUT);

  pinMode(REL_Vac, OUTPUT);

  pinMode(SIGError, OUTPUT);
  pinMode(BUSError, OUTPUT);
  pinMode(xbeError, OUTPUT);

  // Set default values
  digitalWrite(REL_Vac,  LOW);  // turn off REL_Vac
  digitalWrite(SIGError, HIGH); // turn Error SIGnal on

  digitalWrite(BUSError, HIGH); // turn the LED ON (init start)
  digitalWrite(xbeError, HIGH); // turn the LED ON (Pin 13)

  digitalWrite(STEPS_G6, LOW);  // turn off SM
  digitalWrite(STEPS_G7, LOW);  // turn off SM
  digitalWrite(STEPS_G8, LOW);  // turn off SM
  digitalWrite(STEPS_G9, LOW);  // not on ES & turn off SM

  digitalWrite(DIR_G6, LOW);    // turn off SM
  digitalWrite(DIR_G7, LOW);    // turn off SM
  digitalWrite(DIR_G8, LOW);    // turn off SM
  digitalWrite(DIR_G9, LOW);    // not on ES & turn off SM

  runner.init();
  runner.addTask(tC);
  runner.addTask(tB);
  runner.addTask(tR);
  runner.addTask(tGC);
  runner.addTask(tGH);
  runner.addTask(tGM);

  Serial.print("+++"); //Starting the request of IDENT
  tC.enable();
}

// FUNCTIONS (Taesks) ----------------------------
void checkXbee() {
  if (IDENT.startsWith("BGATE") && plplpl == 2) {
    ++plplpl;
    tB.enable();
    digitalWrite(xbeError, LOW); // turn the LED off (Programm start)
  }
}

void retryPOR() {
  if (getTime < porTime * 5) {
    Serial.println(String(IDENT) + ";POR");
    ++getTime;
    tB.setInterval(TASK_SECOND * getTime);
  }
  else if (getTime == 255) {
    tR.setIterations(repMES);
    digitalWrite(BUSError, LOW); // turn the LED off (Programm start)
    tB.disable();
    tC.setCallback(gateStart);
    tC.restart();
    waitGO = 30;  // sec
  }
}

// Task repeatMES: ------------------------
void repeatMES() {
  // --repeat messages from machines
  Serial.println(String(SFMes));
}

// Task Gate start: ------------------------
void gateStart() {
  gate6O = digitalRead(EndPoG6O);
  gate6C = digitalRead(EndPoG6C);
  gate7O = digitalRead(EndPoG7O);
  gate7C = digitalRead(EndPoG7C);
  gate8O = digitalRead(EndPoG8O);
  gate8C = digitalRead(EndPoG8C);
  gate9O = digitalRead(EndPoG9O);
  gate9C = digitalRead(EndPoG9C);
  gateHO = digitalHand(EndPoGHO);
  gateHC = digitalHand(EndPoGHC);

  if (!gate6O && gate6C && !gate7O && gate7C && !gate8O && gate8C && !gate9O && gate9C && !gateHO && gateHC) {
    digitalWrite(SIGError, LOW);
    Serial.println("GOK");  // gates ok, all in position
    tC.disable();
    tR.disable();
    tGC.enable();
  } else {
    if (!(!gate6O && gate6C)) Serial.println("ERR:G6C");
    if (!(!gate7O && gate7C)) Serial.println("ERR:G7C");
    if (!(!gate8O && gate8C)) Serial.println("ERR:G8C");
    if (!(!gate9O && gate9C)) Serial.println("ERR:G9C");
    if (!(!gateHO && gateHC)) Serial.println("ERR:GHC");
  }
}

// Task Gates popsition: -------------------
void gateChange() {
  if (digitalRead(EndPoG6O) != gate6O || digitalRead(EndPoG6C) != gate6C) {
    gate6O = digitalRead(EndPoG6O);
    gate6C = digitalRead(EndPoG6C);
    if (logIM6) {
      if (gate6O && !gate6C) {
        open4log6 = 0;
        SFMes = "G6O";
        if (errCount > 0) --errCount;
      } else {
        SFMes = "ERR:G6O";
        if (errCount == 0) ++errCount;
      }
    } else {
      if (!gate6C && open4log6 < 0) {
        open4log6 = waitGO * divTime; // sec
        SFMes = "G6W";  // wait for login
      } else if (!gate6O && gate6C) {
        open4log6 = -1;
        SFMes = "G6C";
        if (errCount > 0) --errCount;
      } else if (!gate6C && open4log6 == 0) {
				SFMes = "ERR:G6C";
        if (errCount == 0) ++errCount;
      }
    }
    Serial.println(SFMes);
    tR.restart();
    tGM.restartDelayed(50);
  }
  if (digitalRead(EndPoG7O) != gate7O || digitalRead(EndPoG7C) != gate7C) {
    gate7O = digitalRead(EndPoG7O);
    gate7C = digitalRead(EndPoG7C);
    if (logIM7) {
      if (gate7O && !gate7C) {
        open4log7 = 0;
        SFMes = "G7O";
        if (errCount > 0) --errCount;
      } else {
        SFMes = "ERR:G7O";
        if (errCount == 0) ++errCount;
      }
    } else {
      if (!gate7C && open4log7 < 0) {
        open4log7 = waitGO * divTime; // sec
        SFMes = "G7W";  // wait for login
      } else if (!gate7O && gate7C) {
        open4log7 = -1;
        SFMes = "G7C";
        if (errCount > 0) --errCount;
      } else if (!gate7C && open4log7 == 0) {
				SFMes = "ERR:G7C";
        if (errCount == 0) ++errCount;
      }
    }
    Serial.println(SFMes);
    tR.restart();
    tGM.restartDelayed(50);
  }
  if (digitalRead(EndPoG8O) != gate8O || digitalRead(EndPoG8C) != gate8C) {
    gate8O = digitalRead(EndPoG8O);
    gate8C = digitalRead(EndPoG8C);
    if (logIM8) {
      if (gate8O && !gate8C) {
        open4log8 = 0;
        SFMes = "G8O";
        if (errCount > 0) --errCount;
      } else {
        SFMes = "ERR:G8O";
        if (errCount == 0) ++errCount;
      }
    } else {
      if (!gate8C && open4log8 < 0) {
        open4log8 = waitGO * divTime; // sec
        SFMes = "G8W";  // wait for login
      } else if (!gate8O && gate8C) {
        open4log8 = -1;
        SFMes = "G8C";
        if (errCount > 0) --errCount;
      } else if (!gate8C && open4log8 == 0) {
				SFMes = "ERR:G8C";
        if (errCount == 0) ++errCount;
      }
    }
    Serial.println(SFMes);
    tR.restart();
    tGM.restartDelayed(50);
  }
  if (digitalRead(EndPoG9O) != gate9O || digitalRead(EndPoG9C) != gate9C) {
    gate9O = digitalRead(EndPoG9O);
    gate9C = digitalRead(EndPoG9C);
    if (logIM9) {
      if (gate9O && !gate9C) {
        open4log9 = 0;
        SFMes = "G9O";
        if (errCount > 0) --errCount;
      } else {
        SFMes = "ERR:G9O";
        if (errCount == 0) ++errCount;
      }
    } else {
      if (!gate9C && open4log9 < 0) {
        open4log9 = waitGO * divTime; // sec
        SFMes = "G9W";  // wait for login
      } else if (!gate9O && gate9C) {
        open4log9 = -1;
        SFMes = "G9C";
        if (errCount > 0) --errCount;
      } else if (!gate9C && open4log9 == 0) {
				SFMes = "ERR:G9C";
        if (errCount == 0) ++errCount;
      }
    }
    Serial.println(SFMes);
    tR.restart();
    tGM.restartDelayed(50);
  }
  if (digitalHand(EndPoGHO) != gateHO || digitalHand(EndPoGHC) != gateHC) {
    gateHO = digitalHand(EndPoGHO);
    gateHC = digitalHand(EndPoGHC);
    if (gateHO && !gateHC) {
      Serial.println("GHO");
      tGH.restartDelayed(50);
    } else if (!gateHO && gateHC) {
      Serial.println("GHC");
      tGH.restartDelayed(50);
    }
  }
  if (open4log6 > 0) {
    --open4log6;
    if (!logIM6 && open4log6 == 1 && !gate6C) {
      if (errCount == 0) ++errCount;
      open4log6 = 0;
      SFMes = "ERR:G6C";
      Serial.println(SFMes);
      tR.restart();
      tGM.restartDelayed(50);
    } else if (logIM6 && gate6O && !gate6C) {
      if (errCount > 0) --errCount;
      open4log6 = 0;
      SFMes = "G6O";
      Serial.println(SFMes);
      tR.restart();
      tGM.restartDelayed(50);
    }
  }
  if (open4log7 > 0) {
    --open4log7;
    if (!logIM7 && open4log7 == 1 && !gate7C) {
      if (errCount == 0) ++errCount;
      open4log7 = 0;
      SFMes = "ERR:G7C";
      Serial.println(SFMes);
      tR.restart();
      tGM.restartDelayed(50);
    } else if (logIM7 && gate7O && !gate7C) {
      if (errCount > 0) --errCount;
      open4log7 = 0;
      SFMes = "G7O";
      Serial.println(SFMes);
      tR.restart();
      tGM.restartDelayed(50);
    }
  }
  if (open4log8 > 0) {
    --open4log8;
    if (!logIM8 && open4log8 == 1 && !gate8C) {
      if (errCount == 0) ++errCount;
      open4log8 = 0;
      SFMes = "ERR:G8C";
      Serial.println(SFMes);
      tR.restart();
      tGM.restartDelayed(50);
    } else if (logIM8 && gate8O && !gate8C) {
      if (errCount > 0) --errCount;
      open4log8 = 0;
      SFMes = "G8O";
      Serial.println(SFMes);
      tR.restart();
      tGM.restartDelayed(50);
    }
  }
  if (open4log9 > 0) {
    --open4log9;
    if (!logIM9 && open4log9 == 1 && !gate9C) {
      if (errCount == 0) ++errCount;
      open4log9 = 0;
      SFMes = "ERR:G9C";
      Serial.println(SFMes);
      tR.restart();
      tGM.restartDelayed(50);
    } else if (logIM9 && gate9O && !gate9C) {
      if (errCount > 0) --errCount;
      open4log9 = 0;
      SFMes = "G9O";
      Serial.println(SFMes);
      tR.restart();
      tGM.restartDelayed(50);
    }
  }
  if (dustWaitT > 0) --dustWaitT;
  if (errCount > 0) {
    digitalWrite(SIGError, HIGH);
  } else {
    digitalWrite(SIGError, LOW);
  }
}

// Task Gate HAnd: ---------------------
void gateHA() {
  if (!dustC6 && !dustC7 && !dustC8 && !dustC9) {
    if (errCount == 0 && dustWaitT > 0 && gateHO && !gateHC) ++errCount;
    if (errCount == 0 && dustWaitT <= 0) {
      if (gateHO && !gateHC) {
        digitalWrite(REL_Vac, HIGH);
        dustWaitT = -1;
      } else {
        digitalWrite(REL_Vac, LOW);
        if (dustWaitT == -1) dustWaitT = divTime * 30; // *0,25 sec until next dust on
      }
    } else if (errCount > 0 && !gateHO && gateHC) --errCount;
  }
}

// Task Gate MAchine: ---------------------
void gateMA() {
  if (dustC6 || dustC7 || dustC8 || dustC9) {
    digitalWrite(REL_Vac, HIGH);
  } else {
    digitalWrite(REL_Vac, LOW);
  }
}
// END OF TASKS ---------------------------------

// FUNCTIONS ------------------------------------
// Convert analog signal in digital boolean values
boolean digitalHand(int inputPin) {
  if (analogRead(inputPin) > 512) {
    return 1;
  } else {
    return 0;
  }
}
// End Funktions --------------------------------

// Funktions Serial Input (Event) ---------------
void evalSerialData() {
  inStr.toUpperCase();

  if (inStr.startsWith("OK")) {
    if (plplpl == 0) {
      ++plplpl;
      Serial.println("ATNI");
    } else {
      ++plplpl;
    }
  }

  if (inStr.startsWith("BGATE")) {
    Serial.println("ATCN");
    IDENT = inStr;
  }

  if (inStr.startsWith("TIME")) { // return TIME
    getTime = 255;
  }

  if (inStr.startsWith("SETRT") && inStr.length() == 6) { // set repeat messages
    tR.setIterations(inStr.substring(5).toInt());
  }

  if (inStr.startsWith("SETWT") && inStr.length() <=7) { // set repeat messages
    waitGO = inStr.substring(5).toInt();
  }

  // Blast gate controll
  if (inStr.startsWith("LI")) {
    gateNR = inStr.substring(2, 3).toInt();
    switch (gateNR) {
      case 6:
        if (!logIM6) {
          logIM6 = HIGH;
          if (!gate6O) {
            if (errCount == 0) ++errCount;
            SFMes = "ERR:G6O";
          }
        }
        break;
      case 7:
        if (!logIM7) {
          logIM7 = HIGH;
          if (!gate7O) {
            if (errCount == 0) ++errCount;
            SFMes = "ERR:G7O";
          }
        }
        break;
      case 8:
        if (!logIM8) {
          logIM8 = HIGH;
          if (!gate8O) {
            if (errCount == 0) ++errCount;
            SFMes = "ERR:G8O";
          }
        }
        break;
      case 9:
        if (!logIM9) {
          logIM9 = HIGH;
          if (!gate9O) {
            if (errCount == 0) ++errCount;
            SFMes = "ERR:G9O";
          }
        }
        break;
      }
    if (errCount > 0) {
      Serial.println(SFMes);
      tR.restart();
    }
  }

  if (inStr.startsWith("LO")) {
    gateNR = inStr.substring(2, 3).toInt();
    switch (gateNR) {
      case 6:
        if (logIM6) {
          logIM6 = LOW;
          if (!gate6C) {
            if (errCount == 0) ++errCount;
            SFMes = "ERR:G6C";
          }
        }
        break;
      case 7:
        if (logIM7) {
          logIM7 = LOW;
          if (!gate7C) {
            if (errCount == 0) ++errCount;
            SFMes = "ERR:G7C";
          }
        }
        break;
      case 8:
        if (logIM8) {
          logIM8 = LOW;
          if (!gate8C) {
            if (errCount == 0) ++errCount;
            SFMes = "ERR:G8C";
          }
        }
        break;
      case 9:
        if (logIM9) {
          logIM9 = LOW;
          if (!gate9C) {
            if (errCount == 0) ++errCount;
            SFMes = "ERR:G9C";
          }
        }
        break;
    }
    if (errCount > 0) {
      Serial.println(SFMes);
      tR.restart();
    }
  }

  if (inStr.startsWith("DO")) {
    gateNR = inStr.substring(2, 3).toInt();
    switch (gateNR) {
      case 6:
        if (gate6O && !gate6C && logIM6 && !dustC6) dustC6 = HIGH;
        break;
      case 7:
        if (gate7O && !gate7C && logIM7 && !dustC7) dustC7 = HIGH;
        break;
      case 8:
        if (gate8O && !gate8C && logIM8 && !dustC8) dustC8 = HIGH;
        break;
      case 9:
        if (gate9O && !gate9C && logIM9 && !dustC9) dustC9 = HIGH;
        break;
    }
    tGM.restartDelayed(75);
  }

  if (inStr.startsWith("DF")) {
    gateNR = inStr.substring(2, 3).toInt();
    switch (gateNR) {
      case 6:
        if (gate6O && !gate6C && logIM6 && dustC6) dustC6 = LOW;
        break;
      case 7:
        if (gate7O && !gate7C && logIM7 && dustC7) dustC7 = LOW;
        break;
      case 8:
        if (gate8O && !gate8C && logIM8 && dustC8) dustC8 = LOW;
        break;
      case 9:
        if (gate9O && !gate9C && logIM9 && dustC9) dustC9 = LOW;
        break;
    }
    tGM.restartDelayed(75);
  }
}

/* SerialEvent occurs whenever a new data comes in the
  hardware serial RX.  This routine is run between each
  time loop() runs, so using delay inside loop can delay
  response.  Multiple bytes of data may be available.
*/
void serialEvent() {
  char inChar = (char)Serial.read();
  if (inChar == '\x0d') {
    evalSerialData();
    inStr = "";
  } else {
    inStr += inChar;
  }
}
// End Funktions Serial Input -------------------

// PROGRAM LOOP AREA ----------------------------
void loop() {
  runner.execute();
}

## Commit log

2019-01-24 changed names to ue if necessary.
    [Rueckwand.dxf, RÅckwand.dxf]
2019-01-31 changed documents to new version (v17)
    [DichtlippeU.dxf, Front.dxf, MotorhalterSchr.dxf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]
2019-06-04 Changed to metal gates
    [DichtlippeRL.dxf, DichtlippeU.dxf, EndSchalterMount.dxf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]
2019-06-18 Add same drawings for BlastGate mount
    [Reduzierstücke_mit_Halter.stl, SeitenplatteLiAussparung.dxf, SeitenplatteLiGeh.dxf]
2019-08-02 Changed red light blinker (Error)
    [BlastGates.ino]
2019-10-26 Add new pin version (Gate7-9,H changed)
2019-11-05 Send error message ervery second if gate are changing (error detection)
    [BlastGates.ino]
2019-11-08 Update documantation to first release
    [DichtlippeRL.dxf, DichtlippeU.dxf, Front.dxf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]
2019-11-26 Errorcounter changed only 1
    [BlastGates.ino]
